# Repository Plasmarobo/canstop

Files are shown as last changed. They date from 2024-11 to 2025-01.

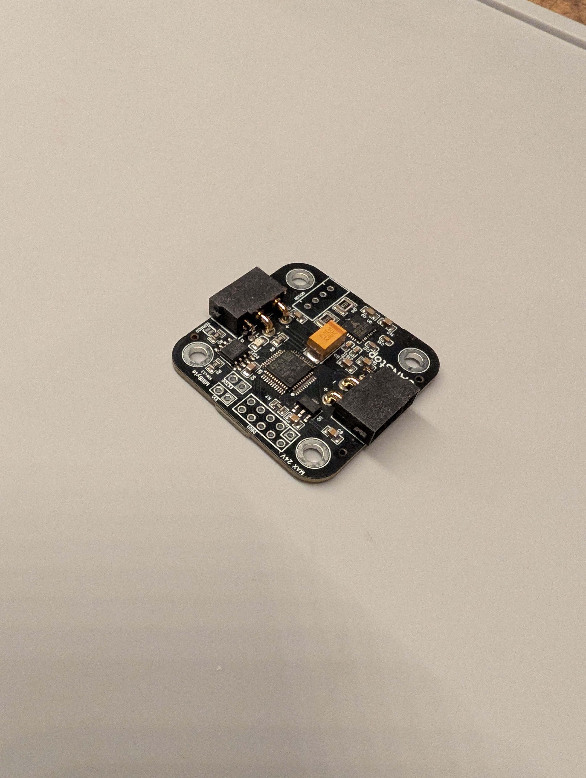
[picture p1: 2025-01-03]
images/PXL_20250103_013551212.jpg

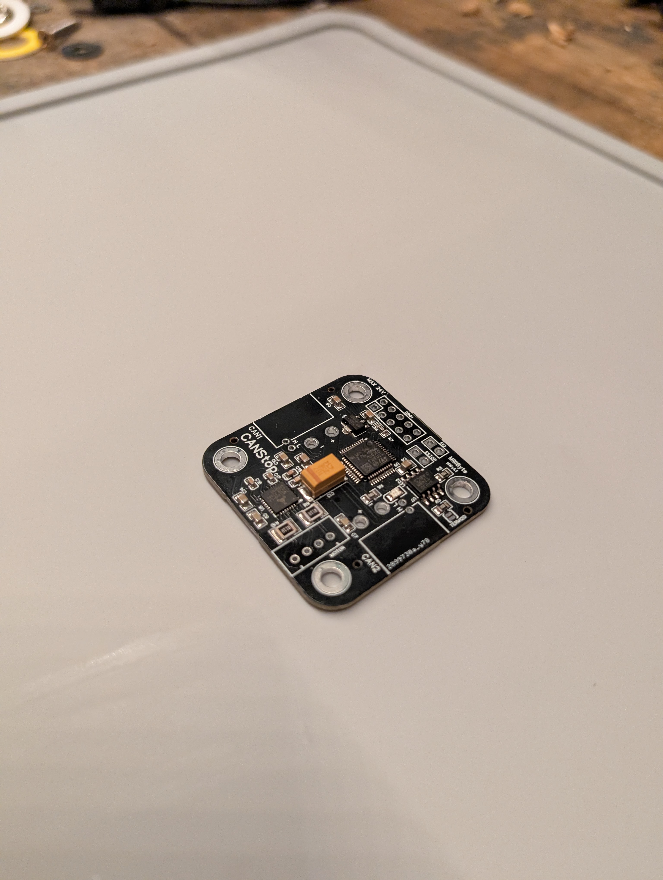
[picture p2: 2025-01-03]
images/PXL_20250103_012944752.jpg

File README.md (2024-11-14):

# canstop
An open hardware CAN motor controller/endstop with NEMA17 mounting

## Klipper Menuconfig
Select STM32F103
CAN Communication on PA12/PA11
Bootloader: optional, if using katapult select 8k

## Katapult Menuconfig
Select STM32F103
CAN Communication on PA12/PA11

## Memory addresses
Use JTAG to flash firmware
Klipper only: @ address 0x8000000
Katapult + Klipper: Katapult @ 0x8000000, Klipper @ 0x8002000

## Klipper Example config
```
[mcu CANStop0]
canbus_uuid: xxxxxxxx

[output_pin CANStop0_led]
pin: CANStop0: PA0

[led CANStop0_led]
green_pin: CANStop0: PA0
cycle_time: 1
hardware_pwm: True

[stepper_a]
step_pin: CANStop0: PB8
enable_pin: CANStop0: PA8
dir_pin: CANStop0: PB7
endstop_pin: CANStop0: PB12

[temperature_sensor]
sensor_type: mcu
sensor_temperature1:
sensor_adc1:
```

# Hardware Description
At the core is an STM32F103C8T6.
The maximum input voltage is 24V, regulated by an HT7533 down to 3.3V for the STM and other devices.
A 120Ohm terminal resistor is on board, with a Normally Open Solder Jumper.
Footprint is desinged for 90 degree angle XT30 2+2 connectors.
## Pin mapping
* BOOT0: Boot 0 debug port
* PA12: CAN_TX
* PA11: CAN_RX
* PA9: UART/PDN for TMC2209
* PA8: TMC2209 Enable pin
* PB8: TMC2209 Step pin
* PB7: TMC2209 DIR pin

* PB15: CAN Standby Pin
* PB13: EIO Pin
* PB12: ESTOP Pin
* PA2: USER UART TX (debug)
* PA3: USER UART RX (debug)
* PA0: LED1 (active low)

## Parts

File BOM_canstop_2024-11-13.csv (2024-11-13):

ID | Name | Designator | Footprint | Quantity | Manufacturer Part | Manufacturer | Supplier | Supplier Part | Price
1 | 10uF | C1,C1,C3,C3,C5,C5 | C0805 | 6 | CL21A106KAYNNNE | SAMSUNG(三星) | LCSC | C15850 | 0.01
2 | 1uF | C2,C2,C4,C4,C20,C20 | C0805 | 6 | CL21B105KBFNNNE | SAMSUNG(三星) | LCSC | C28323 | 0.008
3 | FC-2012HRK-620D | LED1,LED1 | LED0805-R-RD | 2 | NCD0805R1 | 国星光电 | LCSC | C84256 | 0.012
4 | 10kΩ | R1,R1,R3,R3 | R0805 | 4 | 0805W8F1002T5E | UNI-ROYAL(厚声) | LCSC | C17414 | 0.002
5 | 120Ω | R2,R2 | R0805 | 2 | 0805W8F1200T5E | UNI-ROYAL(厚声) | LCSC | C17437 | 0.002
6 | 20Ω | R4,R4 | R0805 | 2 | 0805W8F200JT5E | UNI-ROYAL(厚声) | LCSC | C17544 | 0.002
7 | STM32F103C8T6 | U1,U1 | LQFP-48_L7.0-W7.0-P0.50-LS9.0-BL | 2 | STM32F103C8T6 | ST(意法半导体) | LCSC | C8734 | 1.014
8 | SN65HVD230DR | U2,U2 | SOIC-8_L4.9-W3.9-P1.27-LS6.0-BL | 2 | SN65HVD230DR | TI(德州仪器) | LCSC | C12084 | 0.422
9 | HT7533-1_C14289 | U4,U4 | SOT-89-3_L4.5-W2.5-P1.50-LS4.2-BR | 2 | HT7533-1 | HOLTEK(合泰/盛群) | LCSC | C14289 | 0.112
